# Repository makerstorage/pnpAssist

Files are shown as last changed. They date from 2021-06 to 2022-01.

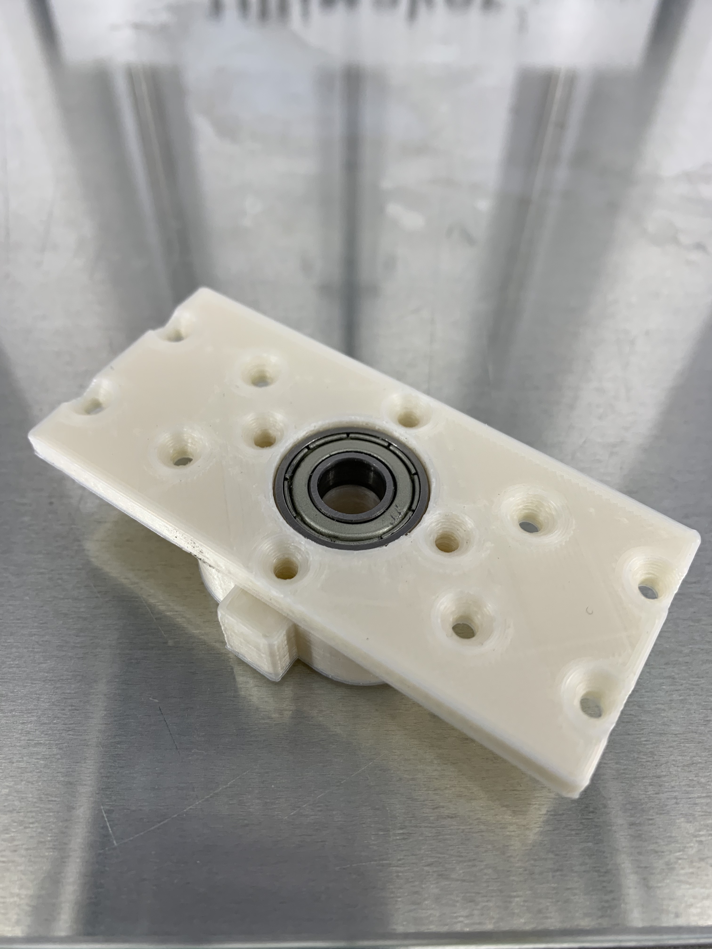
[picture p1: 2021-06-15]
images/IMG_0675.jpeg

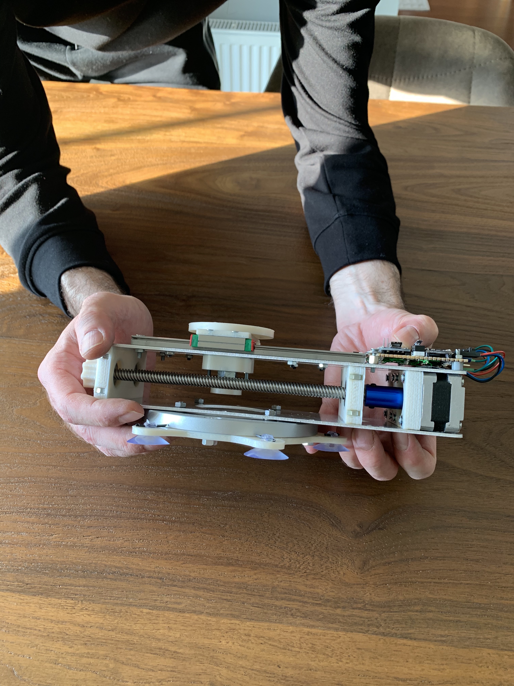
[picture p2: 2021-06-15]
images/IMG_0696.jpeg

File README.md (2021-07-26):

<!-- PROJECT LOGO 
<br />
<p align="center">
  <a href="https://github.com/github_username/repo_name">
    <img src="images/logo.png" alt="Logo" width="80" height="80">
  </a>
-->
  <h3 align="center">PnPAssist</h3>

<!-- ABOUT THE PROJECT -->
## Description
The PnPAssist is an open source innovative CNC table that position the next SMT component with a proper orientation for you to make hand assembly a lot more fun and way more efficient.

PnPAssist is a numerical, precise positioning device that makes tedious and repetitive manual PCB assembly easier for you and prevents you from making mistakes.

<!-- LICENSE -->
## License

GNU GENERAL PUBLIC LICENSE Version 3, 29 June 2007 See `LICENSE` for more information.

<!-- CONTRIBUTING -->
## Contributing

Contributions are what make the open source community such an amazing place to be learn, inspire, and create. Any contributions you make are **greatly appreciated**.

1. Fork the Project
2. Create your Feature Branch (`git checkout -b feature/AmazingFeature`)
3. Commit your Changes (`git commit -m 'Add some AmazingFeature'`)
4. Push to the Branch (`git push origin feature/AmazingFeature`)
5. Open a Pull Request

<!-- CONTACT -->
## Contact

Nuri Erginer - [@nerginer](https://twitter.com/nerginer) 
email - ne@makerstorage.com
Project Link: [Hackaday.io](https://hackaday.io/project/179878-pnpassist)

MakerStorage invests time and resources providing this open source design, please support MakerStorage and open-source hardware by purchasing products from MakerStorage!

Designed by MakerStorage LLC.

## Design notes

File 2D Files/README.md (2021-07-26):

Attention:
You may need to countersink some holes for proper assembly.

Material and production :

Laser cut from 2mm Aluminum

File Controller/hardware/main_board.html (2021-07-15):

Partlist exported from /Users/nerginer/electronics/pnpAssist/Controller/hardware/main_board.sch at 7/12/21 7:53 PM

Qty | Value | Device | Package | Parts | Description | POPULARITY
1 | | J2X5MM | 05C | J1 | Jumper switch 2 x 2.5 mm | 0
1 | | LED0805 | LED-0805 | 12V | LEDs
1 | | ML6 | ML6 | ICSP | HARTING
2 | | PINHD-1X3 | 1X03 | JP1, JP5 | PIN HEADER
6 | | SJ | SJ | SJ1, SJ2, SJ3, SJ4, SJ5, SJ6 | SMD solder JUMPER | 33
1 | 0.1uF | C-USC0805K | C0805K | C2 | CAPACITOR, American symbol
4 | 100nF | CAP0805 | 0805 | C3, C5, C8, C14 | Capacitor
5 | 100uF | CPOL-EUE3.5-8 | E3,5-8 | C4, C6, C7, C9, C10 | POLARIZED CAPACITOR, European symbol
2 | 10K | R-US_R0805 | R0805 | R2, R3 | RESISTOR, American symbol
1 | 10K | RESISTOR | 0805 | R7 | Resistor
1 | 10uF/10V | CPOL-USA/3216-18R | A/3216-18R | C1 | POLARIZED CAPACITOR, American symbol
1 | 16MHZ | CRYSTALHC49S | HC49/S | Q4 | CRYSTAL
2 | 16pf | CAP0805 | 0805 | C12, C13 | Capacitor
1 | 1K | R-US_R0805 | R0805 | R1 | RESISTOR, American symbol
1 | 2.2K | RESISTOR | 0805 | R9 | Resistor
2 | 2133-DRV8825 | 2133-DRV8825 | DRV8825 | IC_A_MOTOR, IC_B_MOTOR | DRV8825 Stepper Motor Driver Carrier, High Current
1 | 2PIN | 2PIN | B2B-PH-K-S | JP4
1 | 330r | R-US_R0805 | R0805 | R10 | RESISTOR, American symbol
1 | 4050D | 4050D | SO16 | IC2 | Hex non-inverting BUFFER
2 | 4PIN | 4PIN | B4B-PH-K-S | MOTOR-A, MOTOR-B
1 | 7805DT | 7805DT | TO252 | IC1 | Positive VOLTAGE REGULATOR
1 | ATMEGA328 | ATMEGA168 | TQFP32-08 | IC5
1 | DISPLAY-OLED-128X64-I2C | DISPLAY-OLED-128X64-I2C | DISPLAY-OLED-128X64-I2C | U$1 | 128x64 Dot Matrix OLED Module based on SSD1306 chip
1 | LP298XS | LP298XS | SOT23-5L | IC3
1 | MICROSD | MICROSD | MICROSD | X1 | Micro-SD / Transflash card holder with SPI pinout
1 | MST2V | MST2V | MSTBV2 | X4 | PHOENIX
1 | RED | LEDCHIP-LED0805 | CHIP-LED0805 | ACT | LED
1 | S_TACT | SPST_TACT-EVQQ2 | EVQ-Q2 | SW_NEXT | SMT 6mm switch, EVQQ2 series

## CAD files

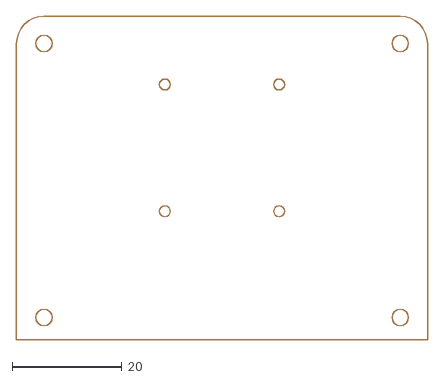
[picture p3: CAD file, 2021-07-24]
Controller/hardware/main_board.dxf
75.0 x 59.0

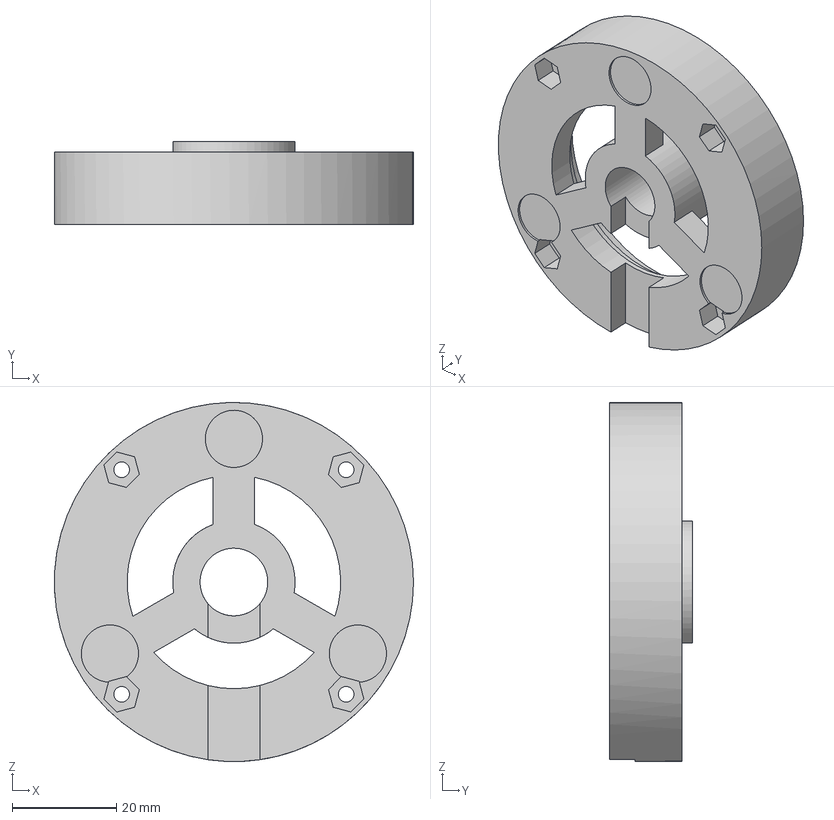
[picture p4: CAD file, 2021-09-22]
V2/3D Files/Step/main_base v29.step
69.0 x 16.0 x 69.0 mm

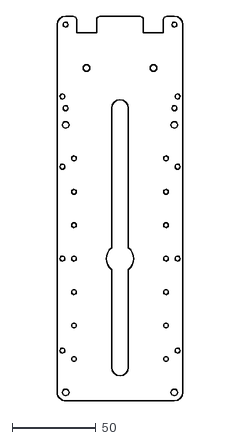
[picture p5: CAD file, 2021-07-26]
2D Files/top_sheet_metal.dxf
75.0 x 230.0

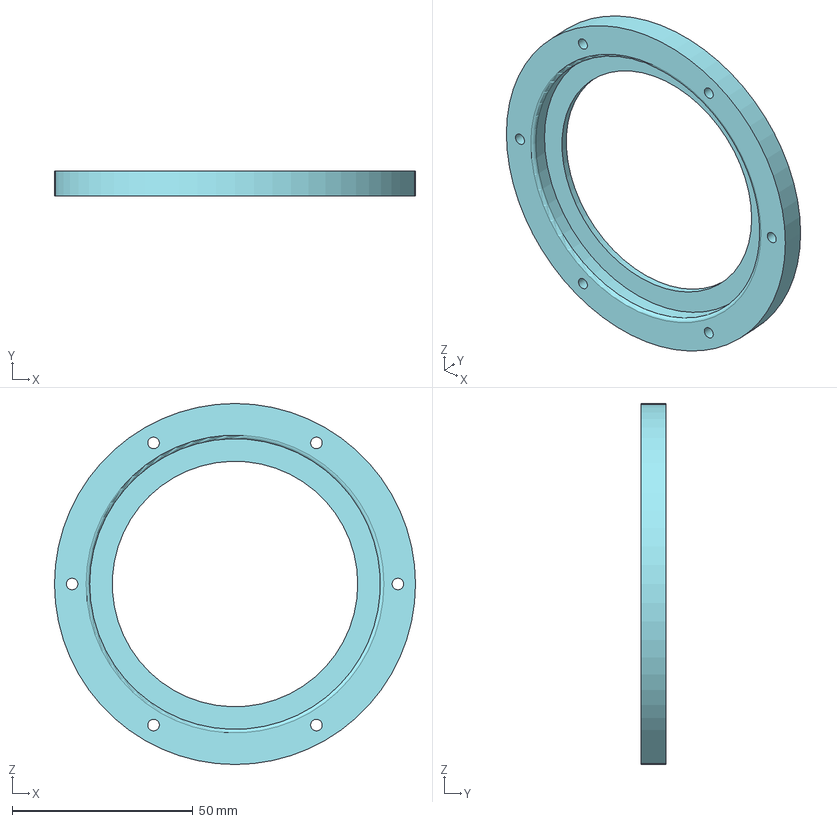
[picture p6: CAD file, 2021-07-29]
3d Files/step/buyuk_rulman_kapak.stp
100.0 x 7.00 x 100.0 mm

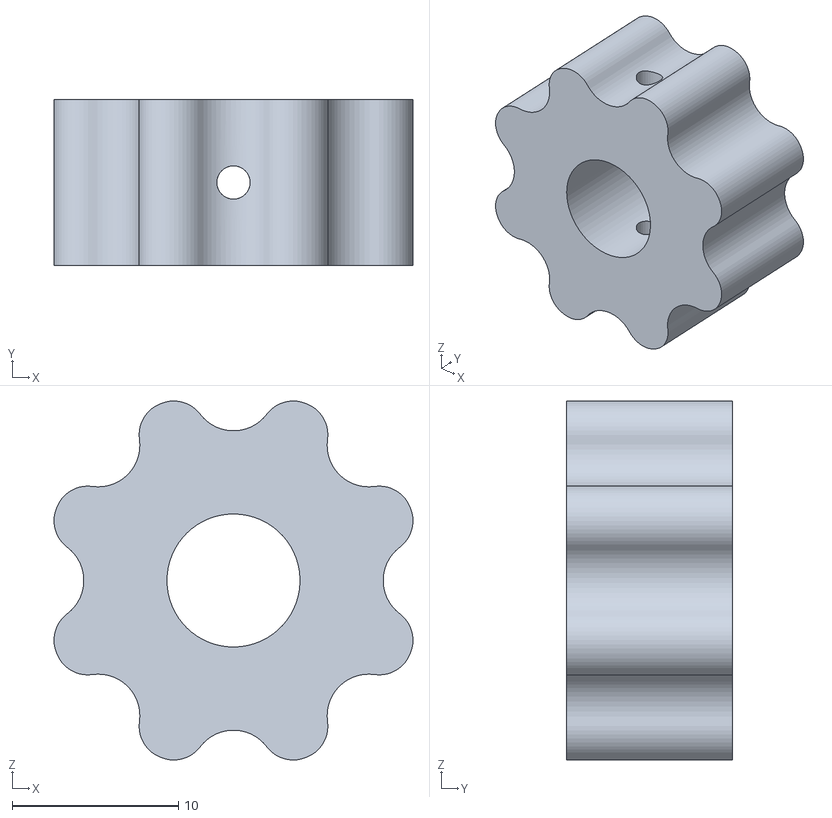
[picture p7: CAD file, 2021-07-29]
3d Files/stl/pnp_assist_tutac v1.stl
21.6 x 10.0 x 21.6

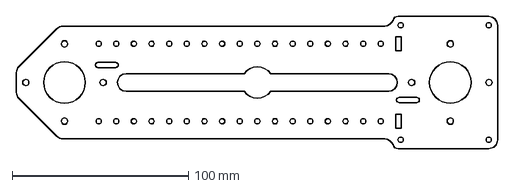
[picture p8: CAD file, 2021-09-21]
V2/2D Files/sac.dxf
272.8 x 75.0 mm

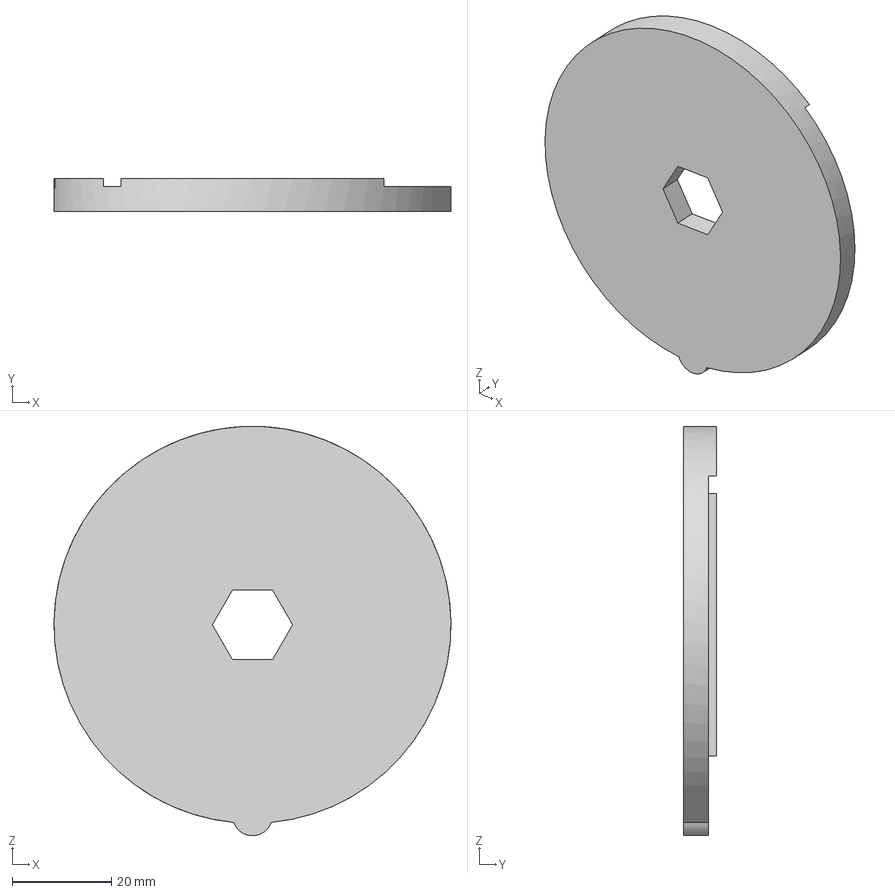
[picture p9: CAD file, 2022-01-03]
V2/3D Files/Step/rotator5.step
80.0 x 6.60 x 82.5 mm

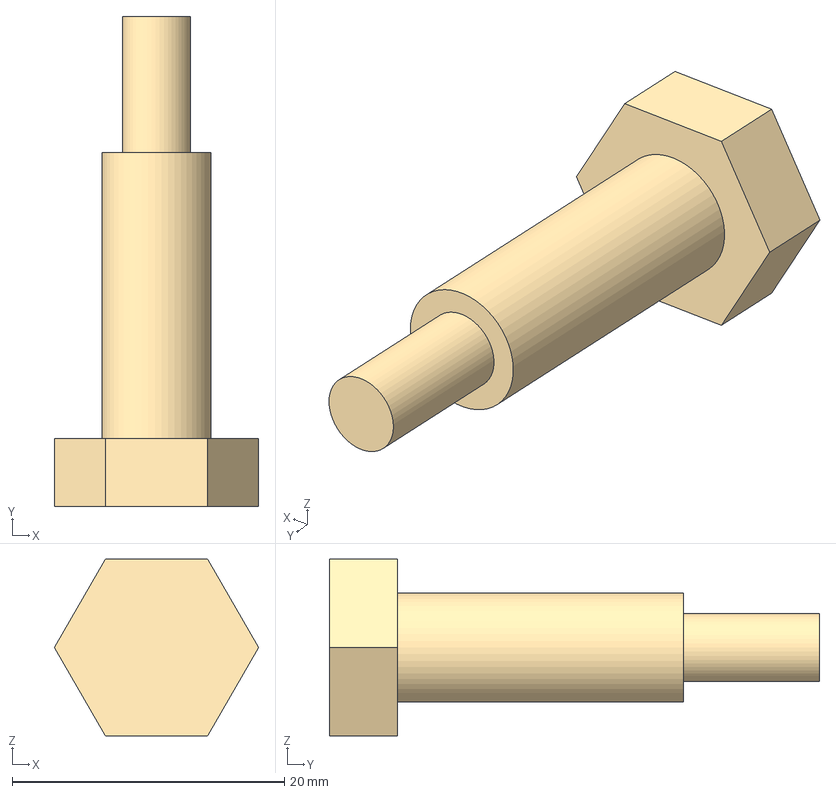
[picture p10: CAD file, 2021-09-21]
V2/CNC/custom_shaft.step
15.0 x 36.0 x 13.0 mm

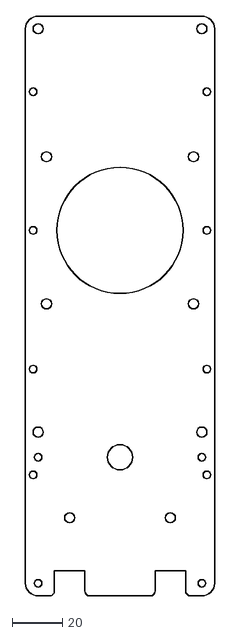
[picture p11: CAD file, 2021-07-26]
2D Files/bottom_sheet_metal.dxf
75.0 x 230.0

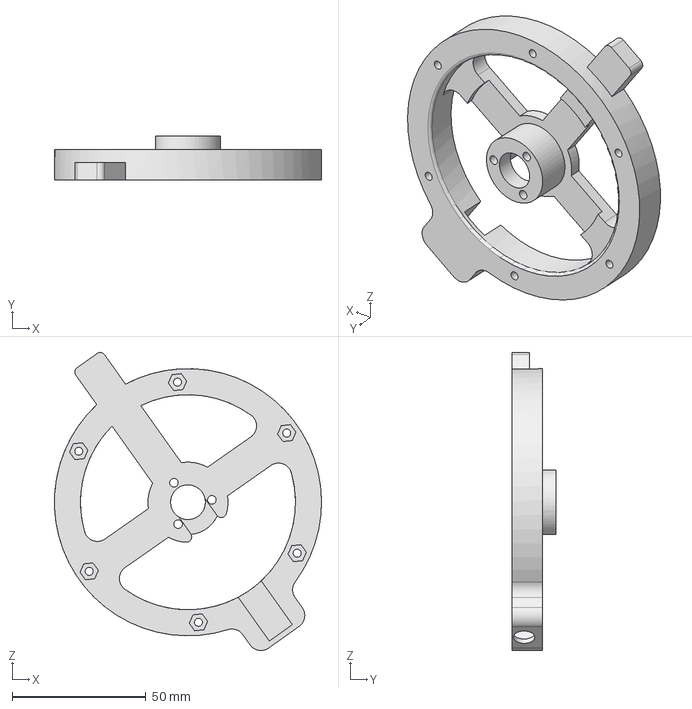
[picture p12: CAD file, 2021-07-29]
3d Files/step/buyuk_rulman_tut.stp
100.0 x 16.5 x 111.6 mm

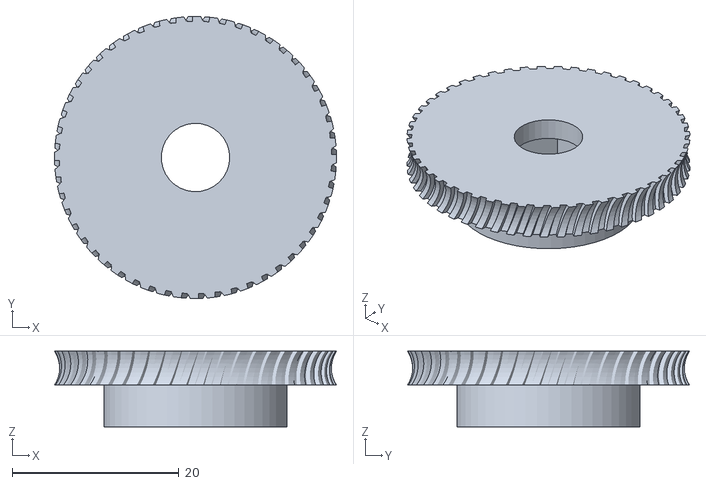
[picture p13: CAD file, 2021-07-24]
3d Files/stl/son_disli_kavisli v2.stl
33.8 x 33.8 x 9.06

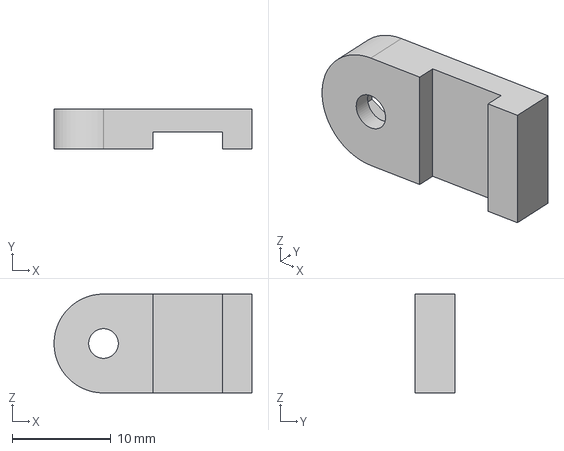
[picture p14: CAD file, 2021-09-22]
V2/3D Files/Step/kablo_bastir v2.step
20.0 x 4.00 x 10.0 mm

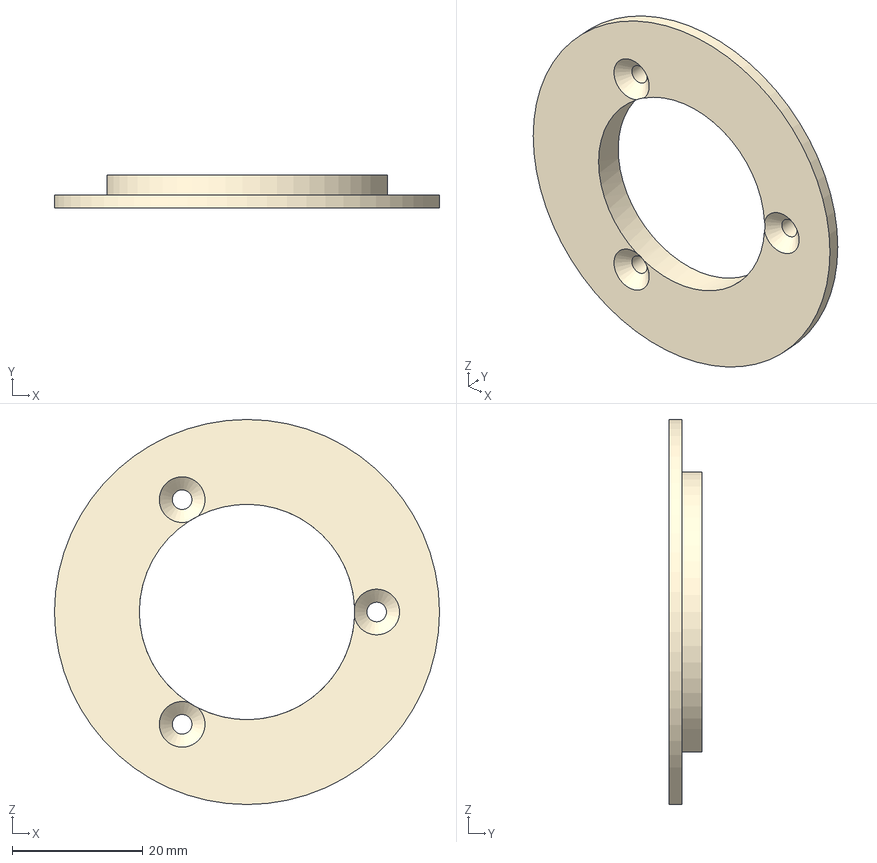
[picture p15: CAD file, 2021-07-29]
3d Files/step/ayak_ust_base.stp
59.0 x 5.00 x 59.0 mm

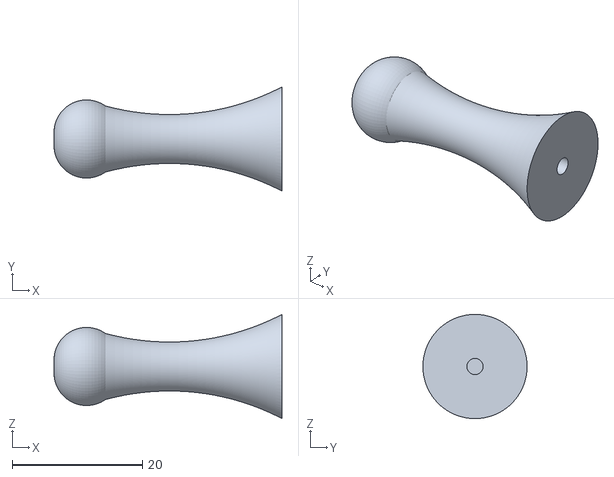
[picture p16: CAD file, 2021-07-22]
3d Files/stl/tutcak.stl
35.0 x 16.0 x 16.0

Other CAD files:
V2/3D Files/Step/yukselti v7.step
3d Files/step/rulmanlik.stp
3d Files/stl/bilezik.stl
V2/3D Files/Step/bearing_cap v2.step
3d Files/step/ayak_ust_base_B.stp
3d Files/step/motor_tut.stp
3d Files/step/rotator3.stp
3d Files/step/rulman_tut_orta.stp
3d Files/step/ust_arabalik.stp
3d Files/step/ust_rulmanlik3.stp
3d Files/stl/ayak_ust_base.stl
3d Files/stl/ayak_ust_base_B.stl
3d Files/stl/buyuk_rulman_kapak.stl
3d Files/stl/buyuk_rulman_tut.stl
3d Files/stl/lead t8 2mm pitch-duz_hex v1.stl
3d Files/stl/motor_tut.stl
3d Files/stl/rotator3.stl
3d Files/stl/rulman_tut.stl
3d Files/stl/rulman_tut_orta.stl
3d Files/stl/rulmanlik.stl
3d Files/stl/ust_arabalik.stl
3d Files/stl/ust_rulmanlik3.stl
V2/3D Files/Step/alt_rulmanlik v13.step
V2/3D Files/Step/arabalik v16.step
V2/3D Files/Step/bearing_inner v14.step
V2/3D Files/Step/carousel2 v7.step
V2/3D Files/Step/clips v2.step
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

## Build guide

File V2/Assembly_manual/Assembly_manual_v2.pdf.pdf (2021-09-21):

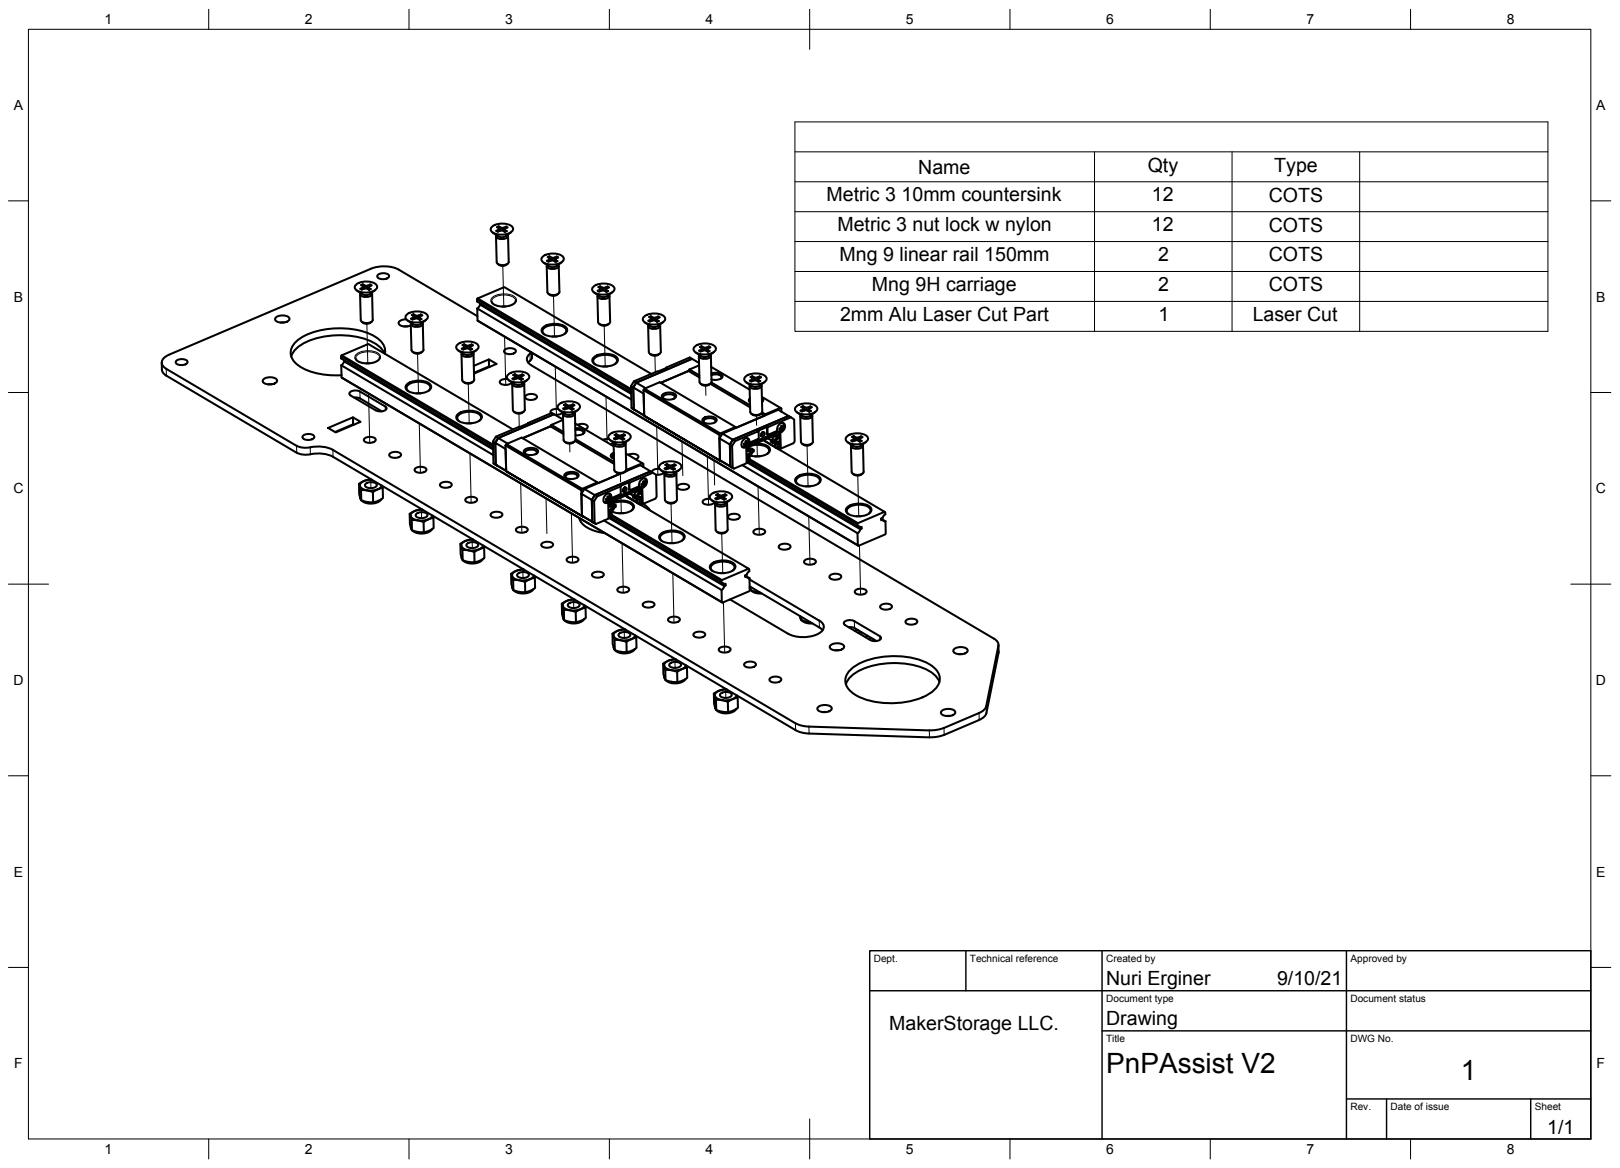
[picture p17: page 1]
Name; Qty; Type; Metric 3 10mm countersink; COTS; Metric 3 nut lock w nylon; Mng 9 linear rail 150mm; Mng 9H carriage; 2mm Alu Laser Cut Part; Laser Cut; Dept.; Technical reference; Created by; Approved by; Document type; Document status; Title; DWG No.; Rev.; Date of issue; Sheet; Drawing; PnPAssist V2; Nuri Erginer; MakerStorage LLC.

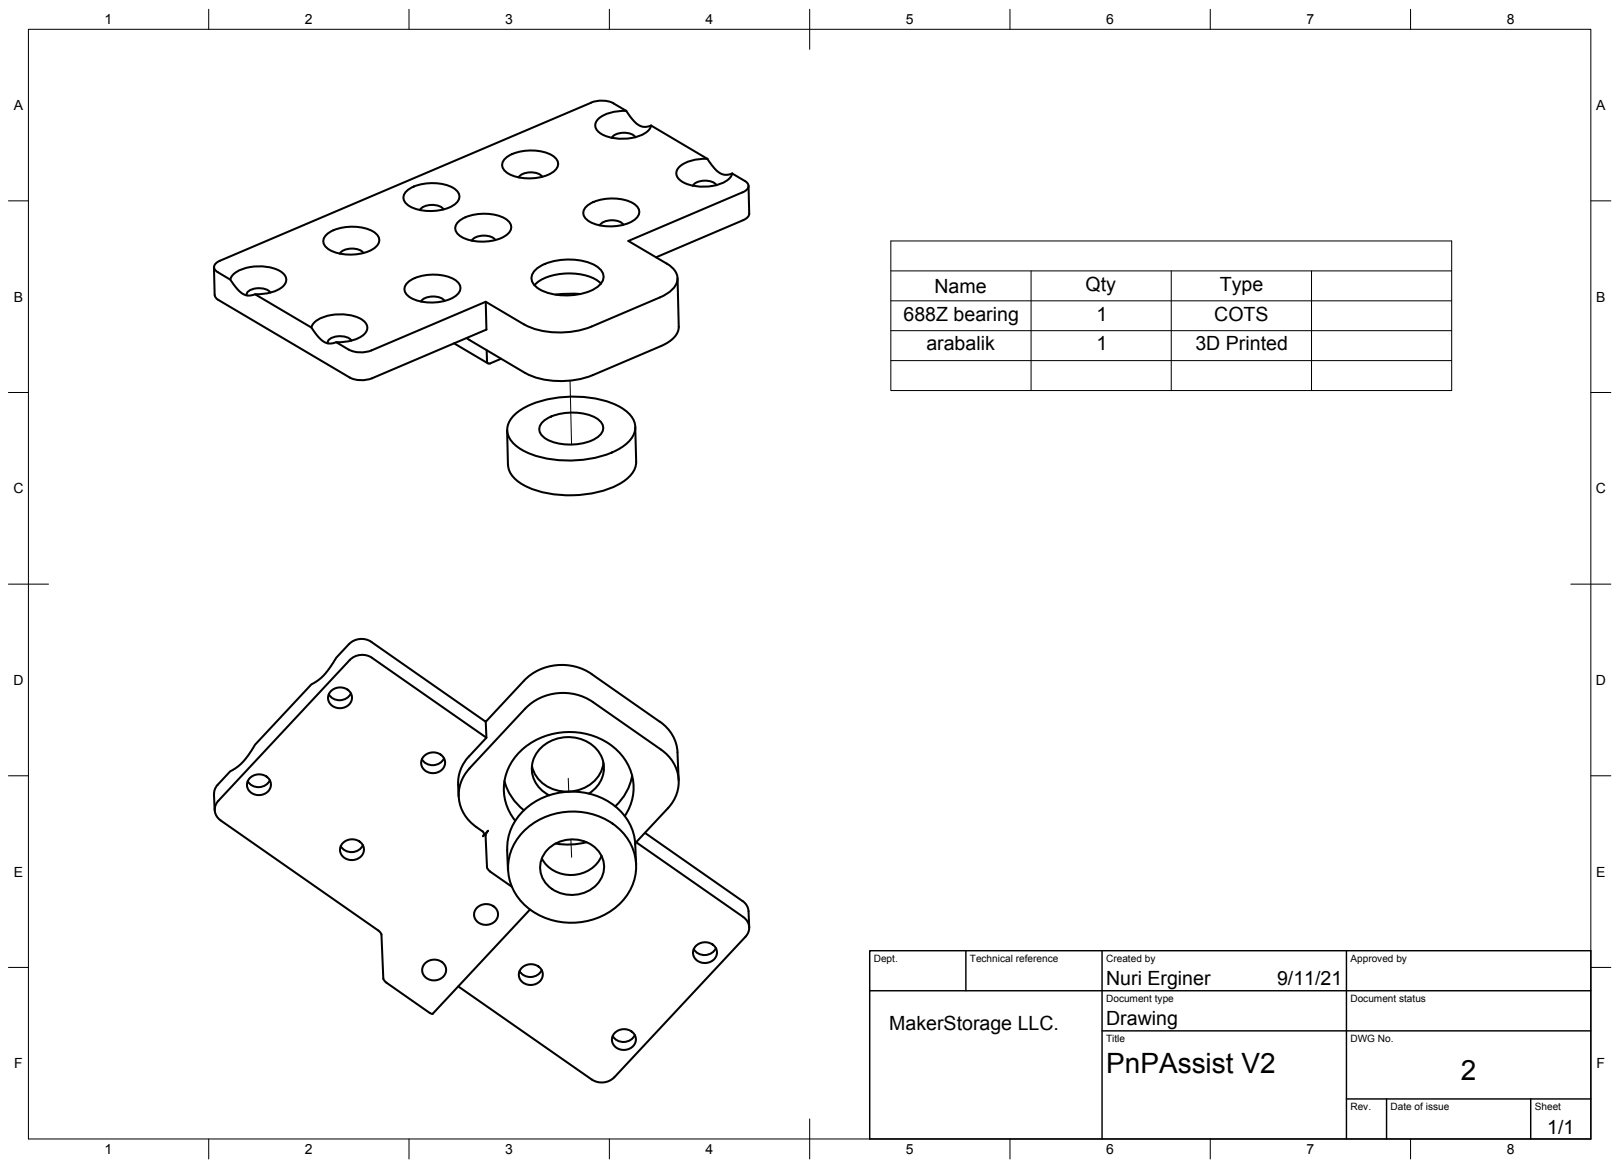
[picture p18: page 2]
Name; Qty; Type; 688Z bearing; COTS; arabalik; 3D Printed; Dept.; Technical reference; Created by; Approved by; Document type; Document status; Title; DWG No.; Drawing; PnPAssist V2; Nuri Erginer; MakerStorage LLC.

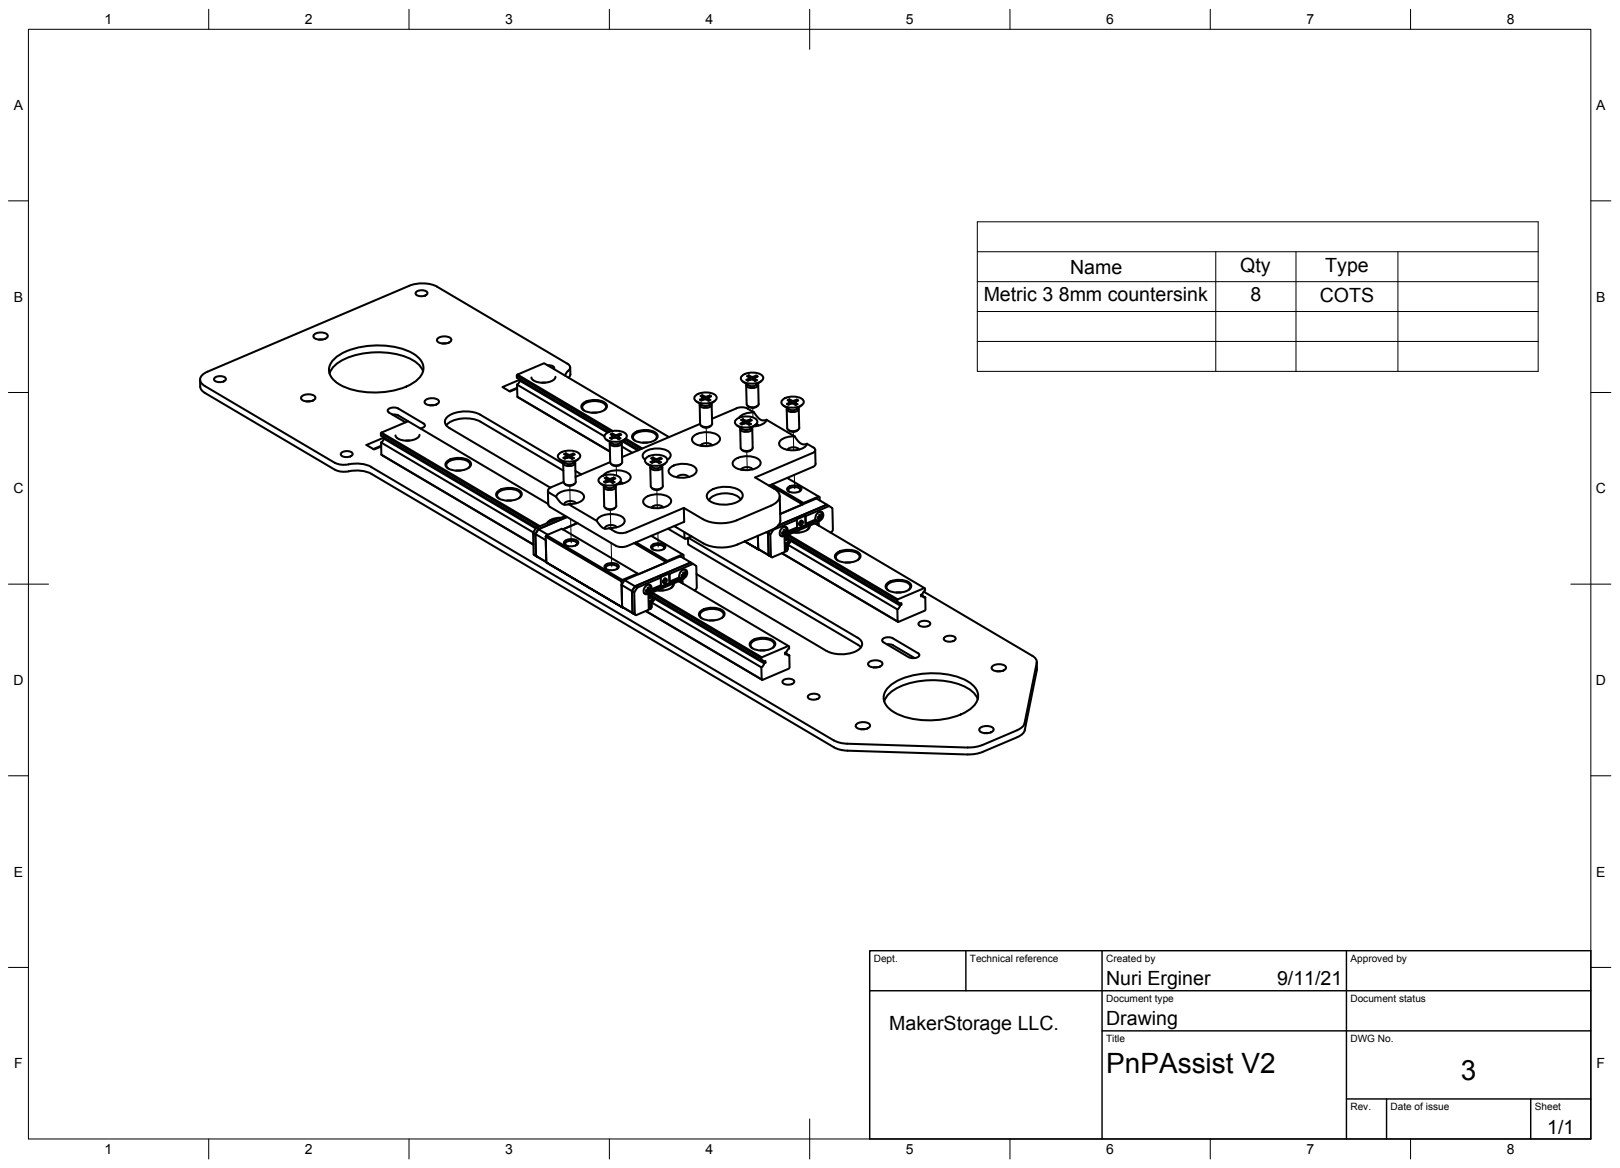
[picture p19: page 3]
Dept.; Technical reference; Created by; Approved by; Document type; Document status; Title; DWG No.; Drawing; PnPAssist V2; Nuri Erginer; Name; Qty; Type; Metric 3 8mm countersink; COTS; MakerStorage LLC.

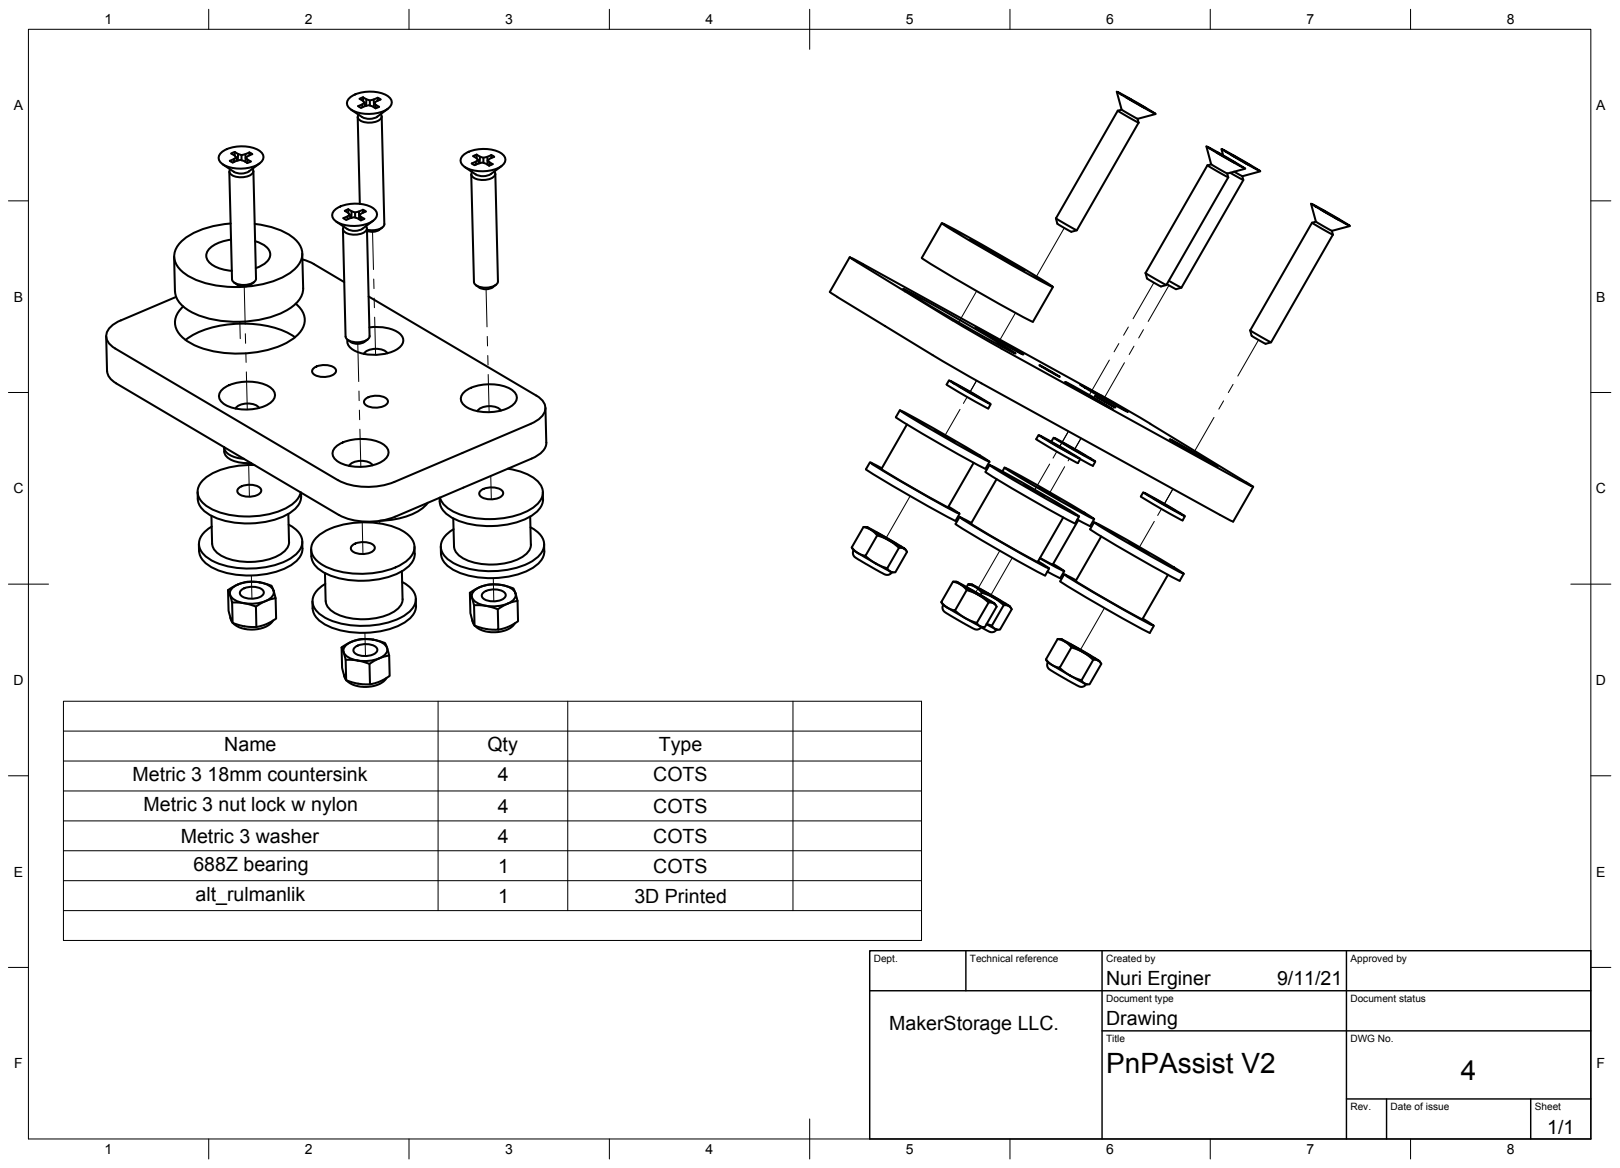
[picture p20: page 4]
Dept.; Technical reference; Created by; Approved by; Document type; Document status; Title; DWG No.; Drawing; PnPAssist V2; Nuri Erginer; alt_rulmanlik; 3D Printed; 688Z bearing; COTS; Metric 3 washer; Metric 3 nut lock w nylon; Metric 3 18mm countersink; Name; Qty; Type; MakerStorage LLC.

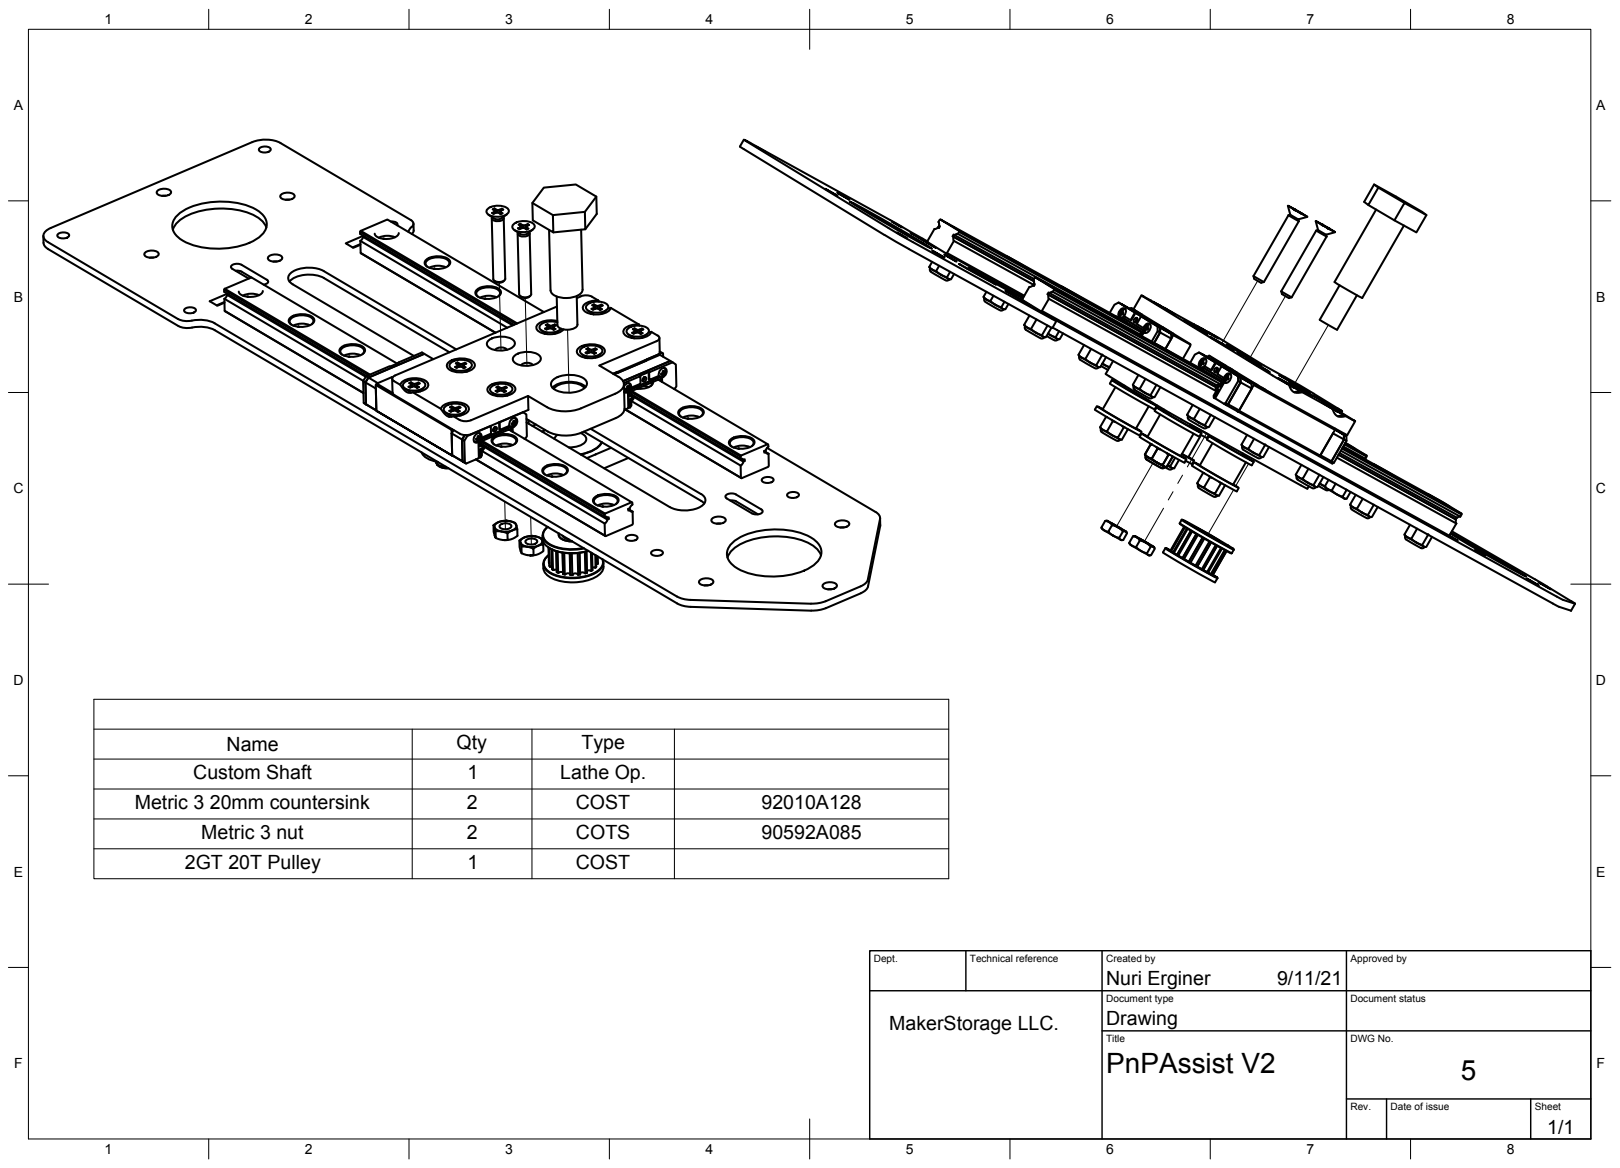
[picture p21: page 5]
Dept.; Technical reference; Created by; Approved by; Document type; Document status; Title; DWG No.; Drawing; PnPAssist V2; Nuri Erginer; Name; Qty; Type; Custom Shaft; Lathe Op.; Metric 3 20mm countersink; COST; Metric 3 nut; COTS; 2GT 20T Pulley; MakerStorage LLC.

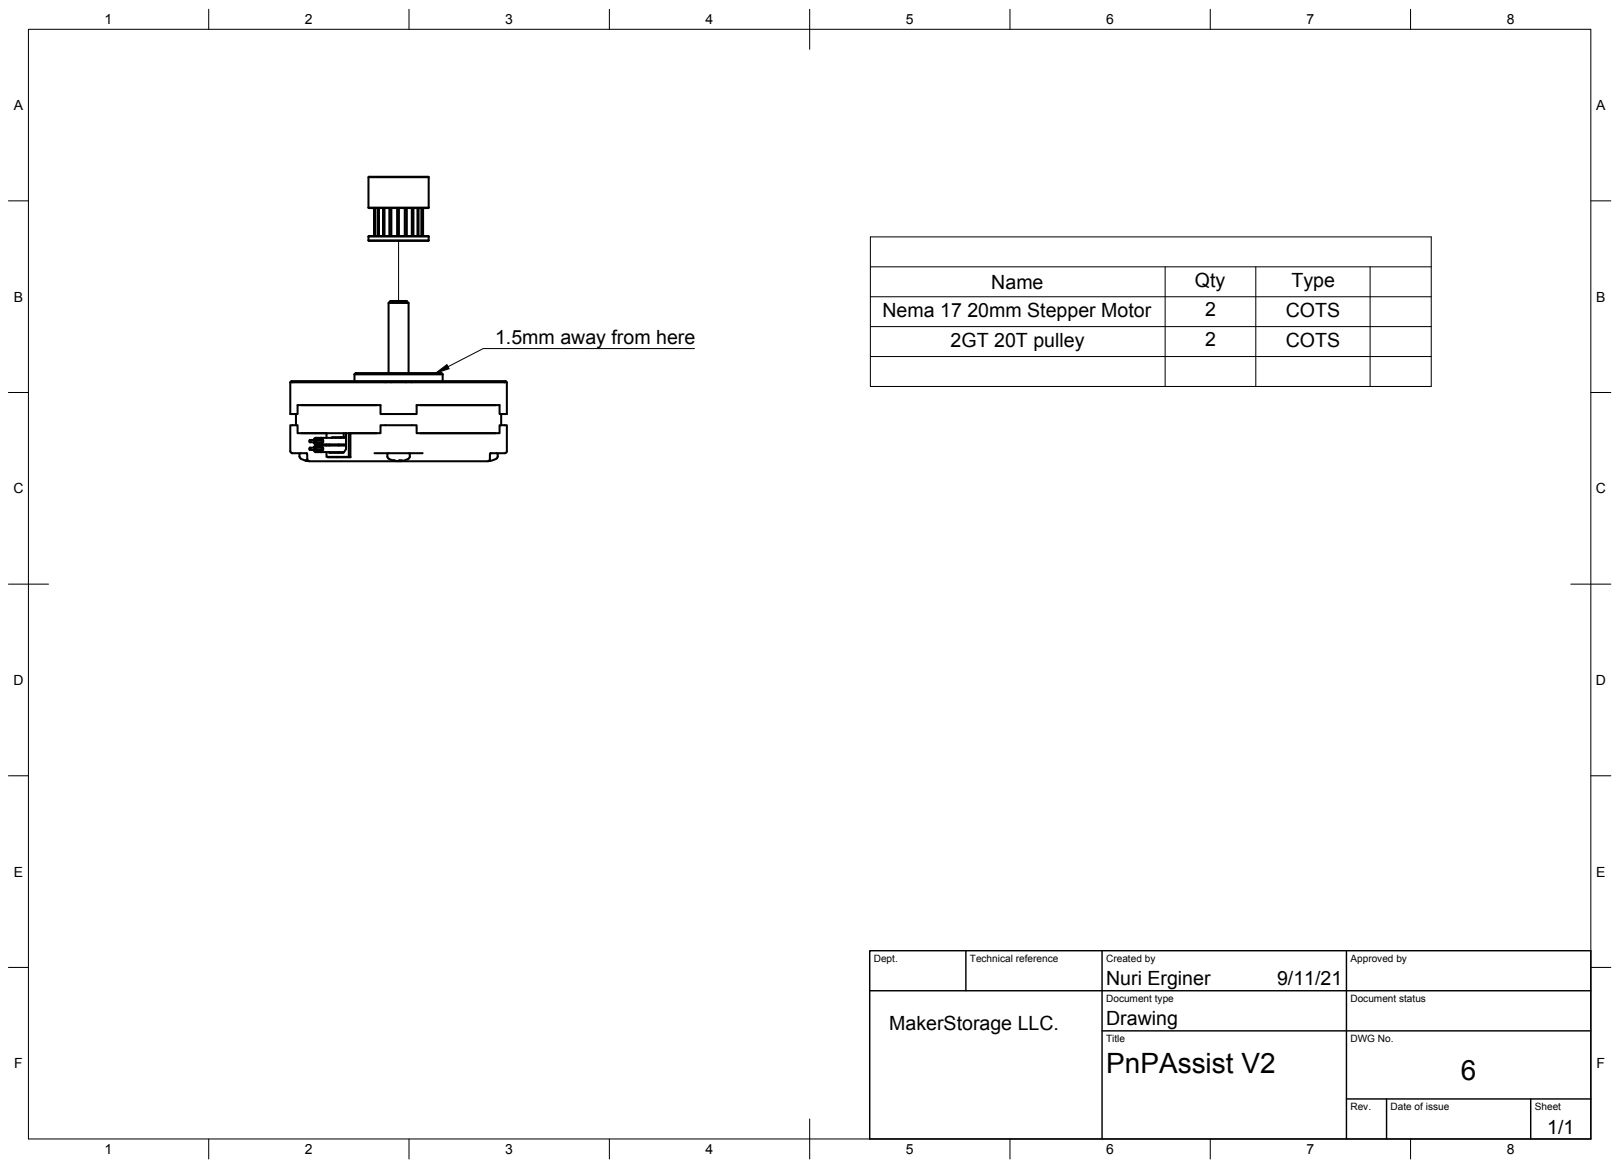
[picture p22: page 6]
Dept.; Technical reference; Created by; Approved by; Document type; Document status; Title; DWG No.; Drawing; PnPAssist V2; Nuri Erginer; Name; Qty; Type; Nema 17 20mm Stepper Motor; COTS; 2GT 20T pulley; MakerStorage LLC.

1.5mm away from here

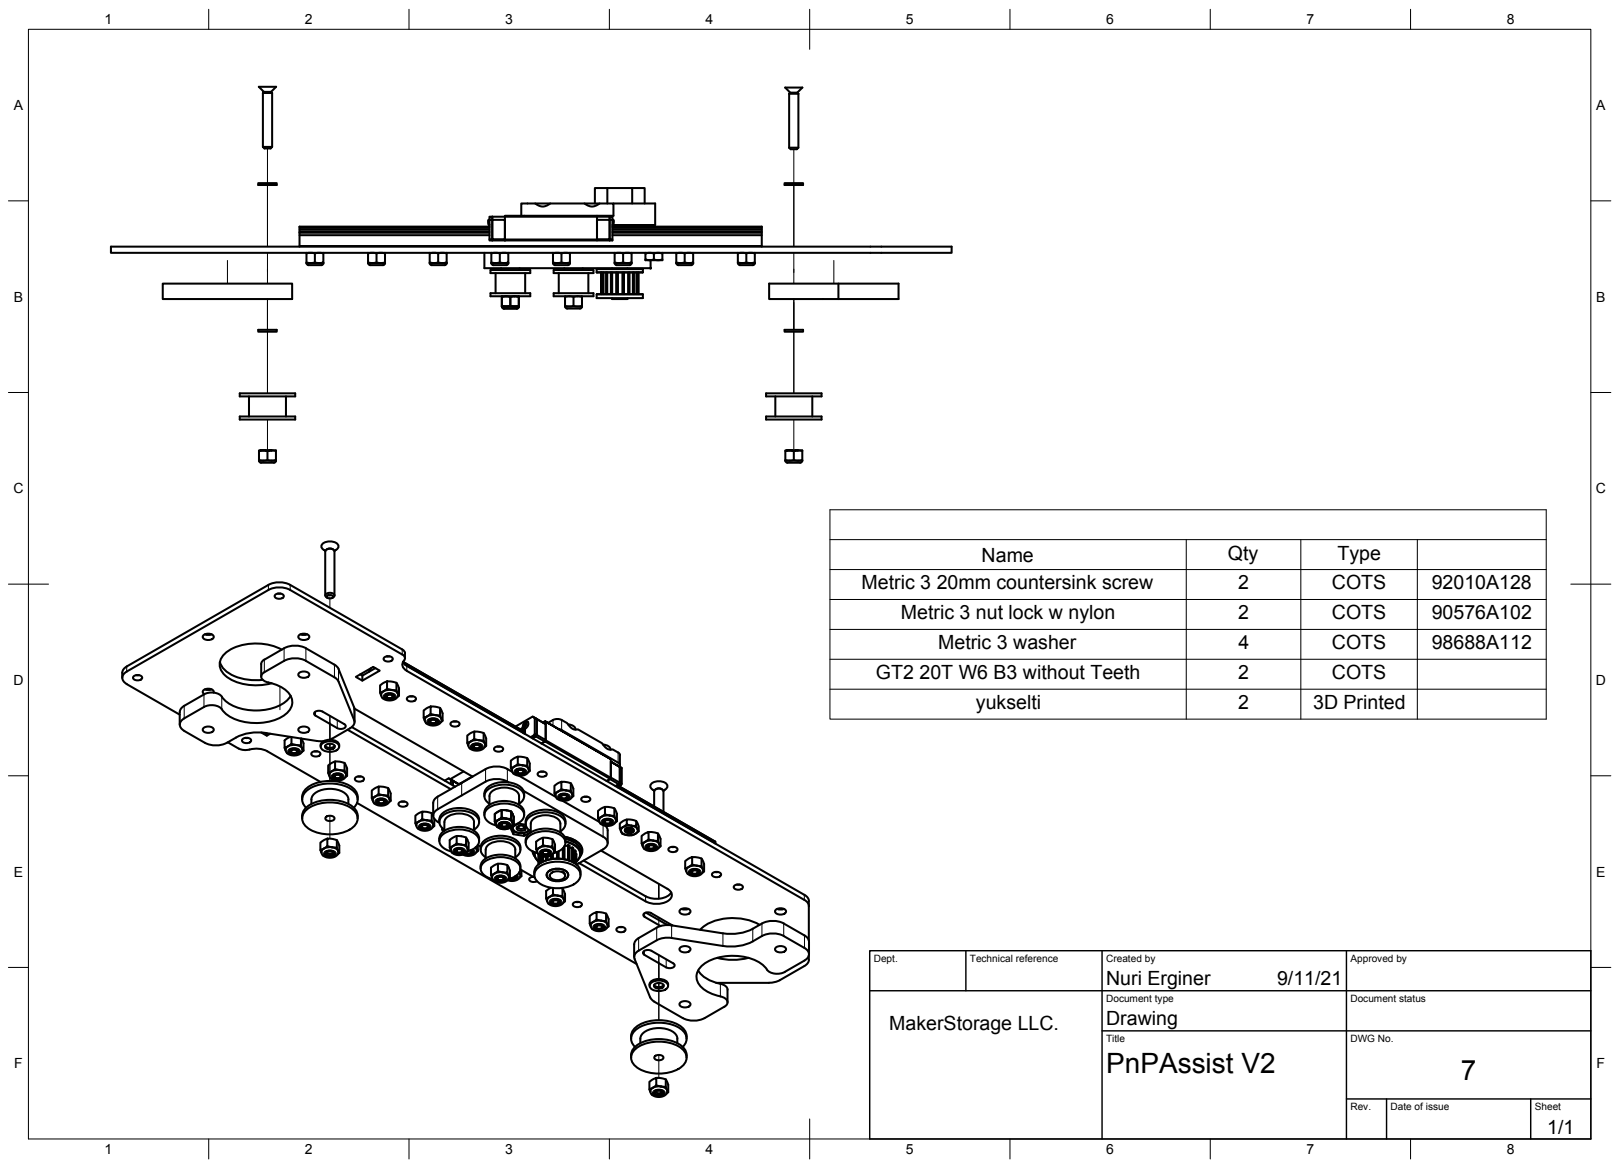
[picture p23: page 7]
Dept.; Technical reference; Created by; Approved by; Document type; Document status; Title; DWG No.; Drawing; PnPAssist V2; Nuri Erginer; Name; Qty; Type; Metric 3 20mm countersink screw; COTS; Metric 3 nut lock w nylon; Metric 3 washer; GT2 20T W6 B3 without Teeth; yukselti; 3D Printed; MakerStorage LLC.

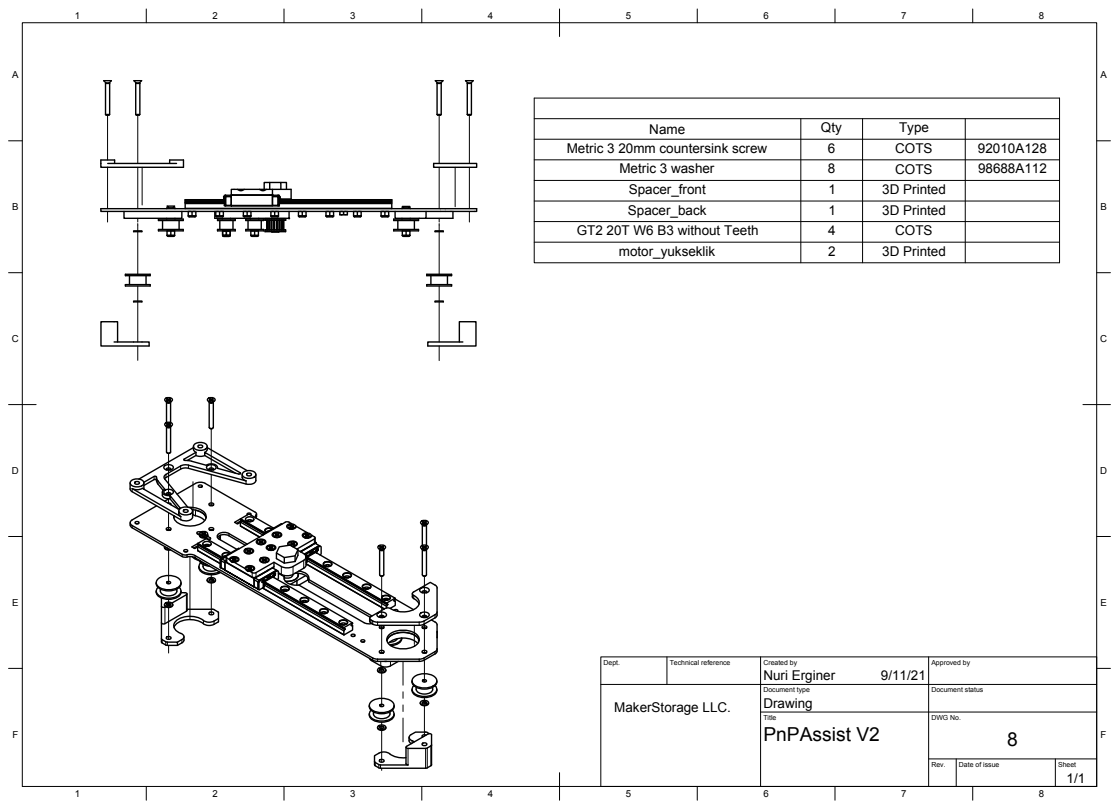
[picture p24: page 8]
Dept.; Technical reference; Created by; Approved by; Document type; Document status; Title; DWG No.; Drawing; PnPAssist V2; Nuri Erginer; Name; Qty; Type; Metric 3 20mm countersink screw; COTS; Metric 3 washer; Spacer_front; 3D Printed; Spacer_back; GT2 20T W6 B3 without Teeth; motor_yukseklik; MakerStorage LLC.

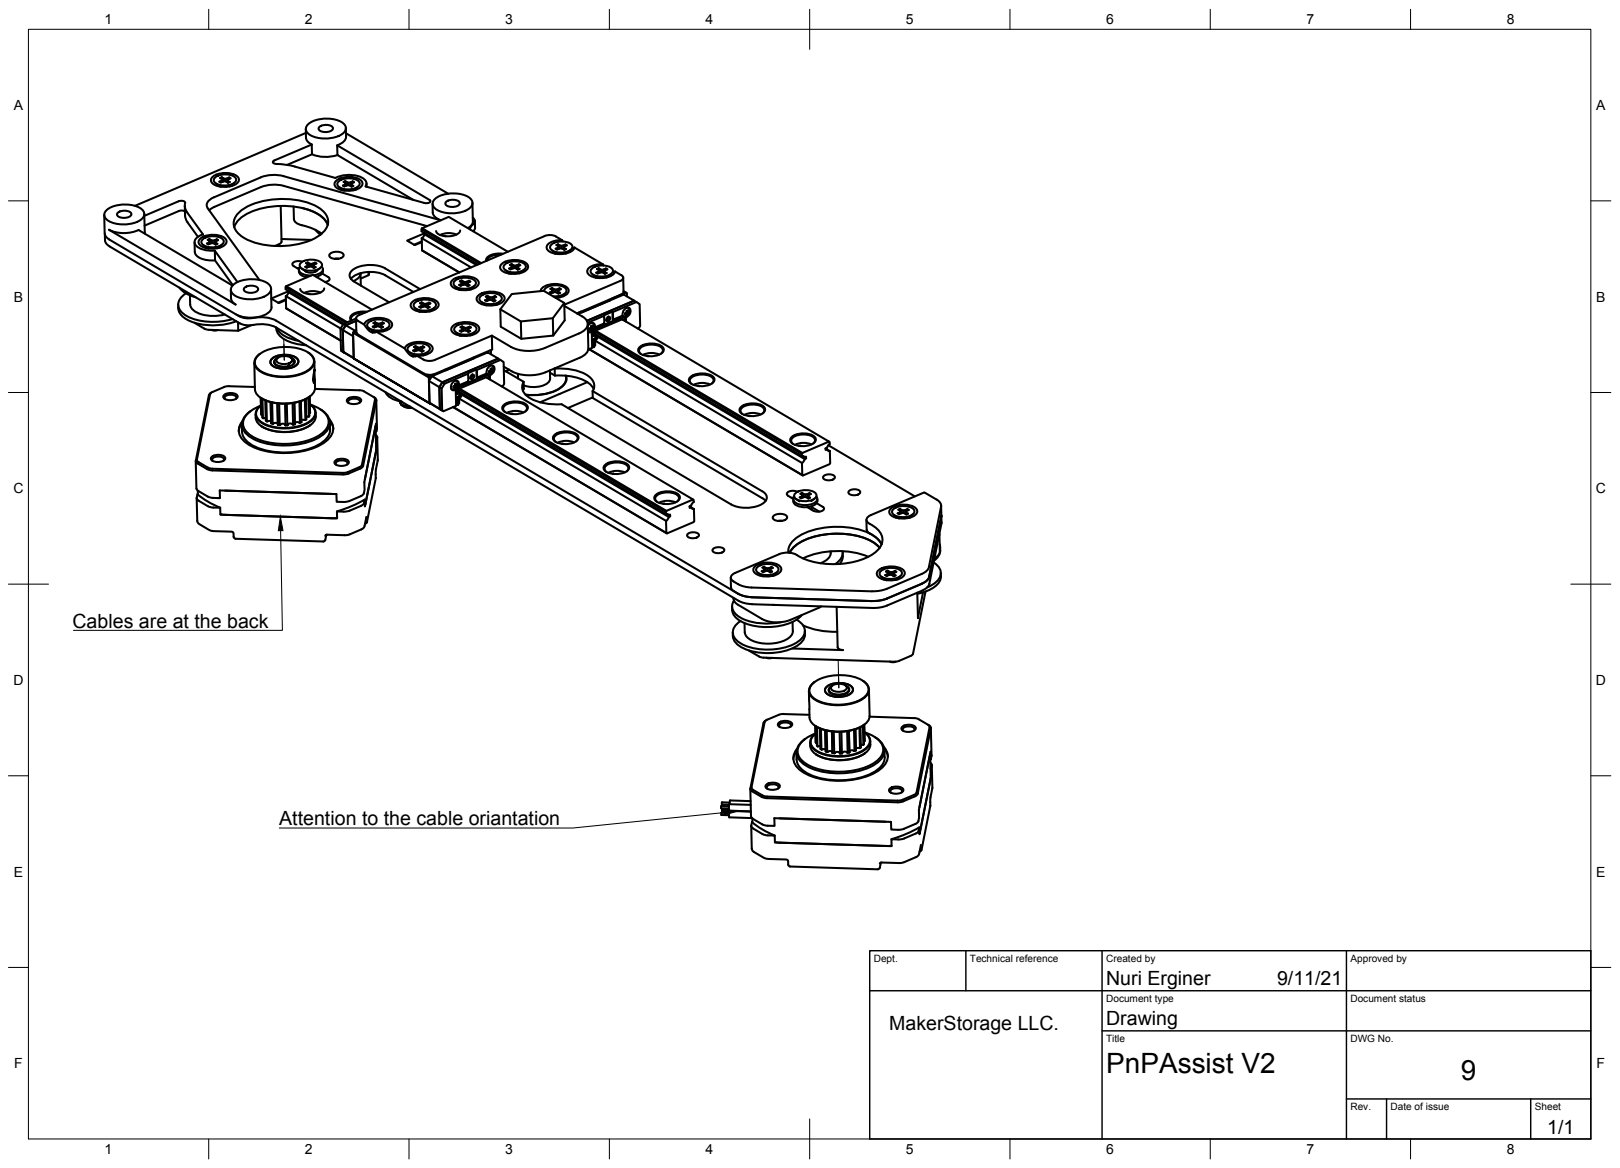
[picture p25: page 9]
Dept.; Technical reference; Created by; Approved by; Document type; Document status; Title; DWG No.; Drawing; PnPAssist V2; Nuri Erginer; MakerStorage LLC.

Cables are at the back

Attention to the cable oriantation

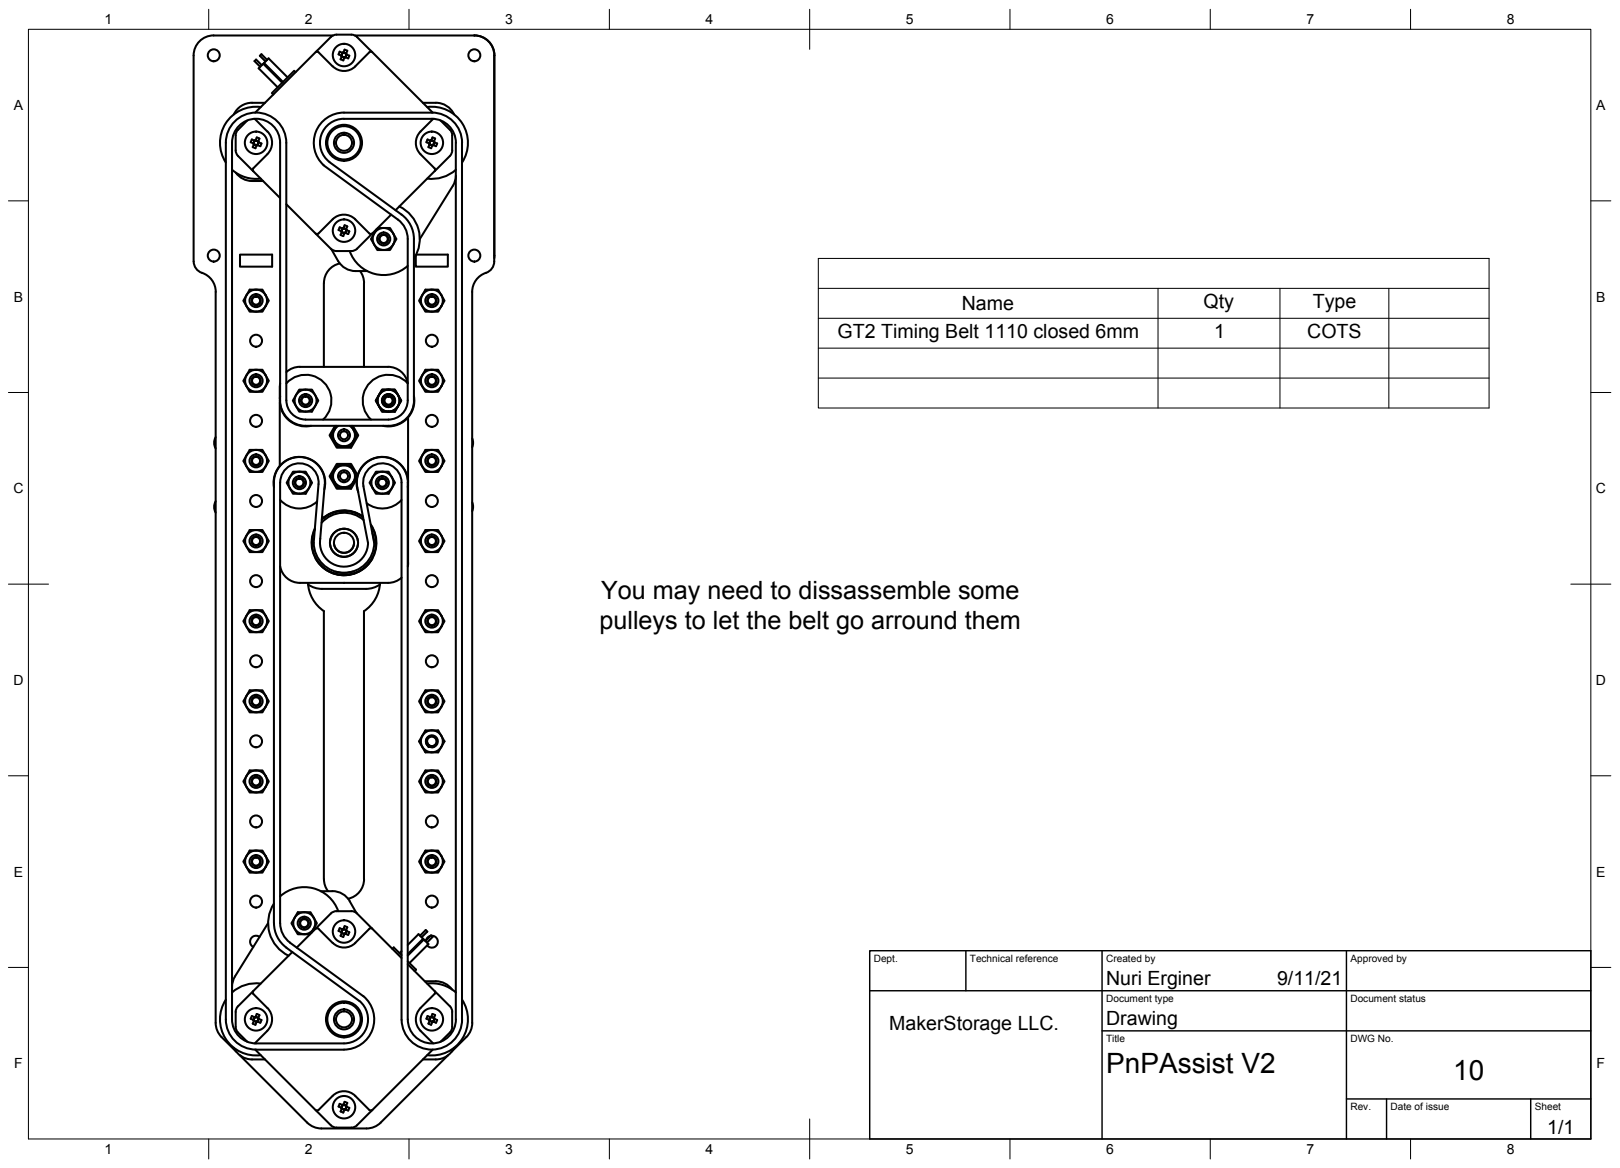
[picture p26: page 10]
Dept.; Technical reference; Created by; Approved by; Document type; Document status; Title; DWG No.; Drawing; PnPAssist V2; Nuri Erginer; Name; Qty; Type; GT2 Timing Belt 1110 closed 6mm; COTS; MakerStorage LLC.

You may need to dissassemble some
pulleys to let the belt go arround them

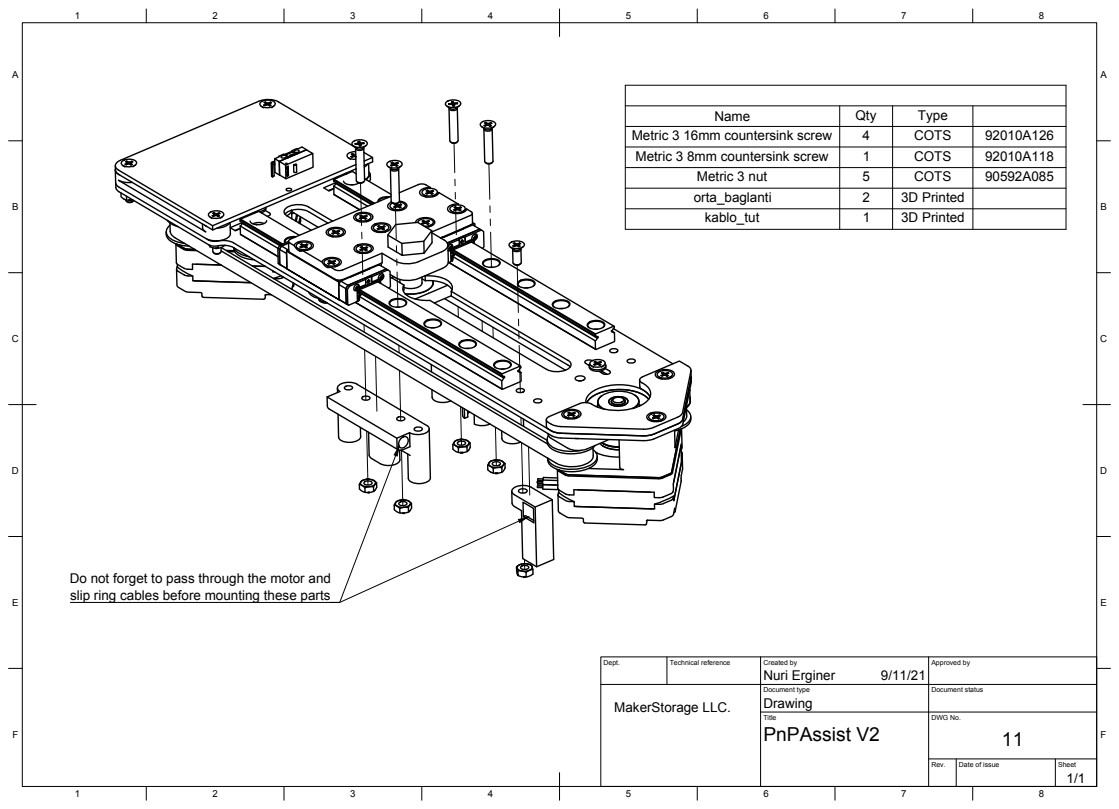
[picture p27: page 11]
Dept.; Technical reference; Created by; Approved by; Document type; Document status; Title; DWG No.; Drawing; PnPAssist V2; Nuri Erginer; Name; Qty; Type; Metric 3 16mm countersink screw; COTS; Metric 3 8mm countersink screw; Metric 3 nut; orta_baglanti; 3D Printed; kablo_tut; MakerStorage LLC.

Do not forget to pass through the motor and
slip ring cables before mounting these parts

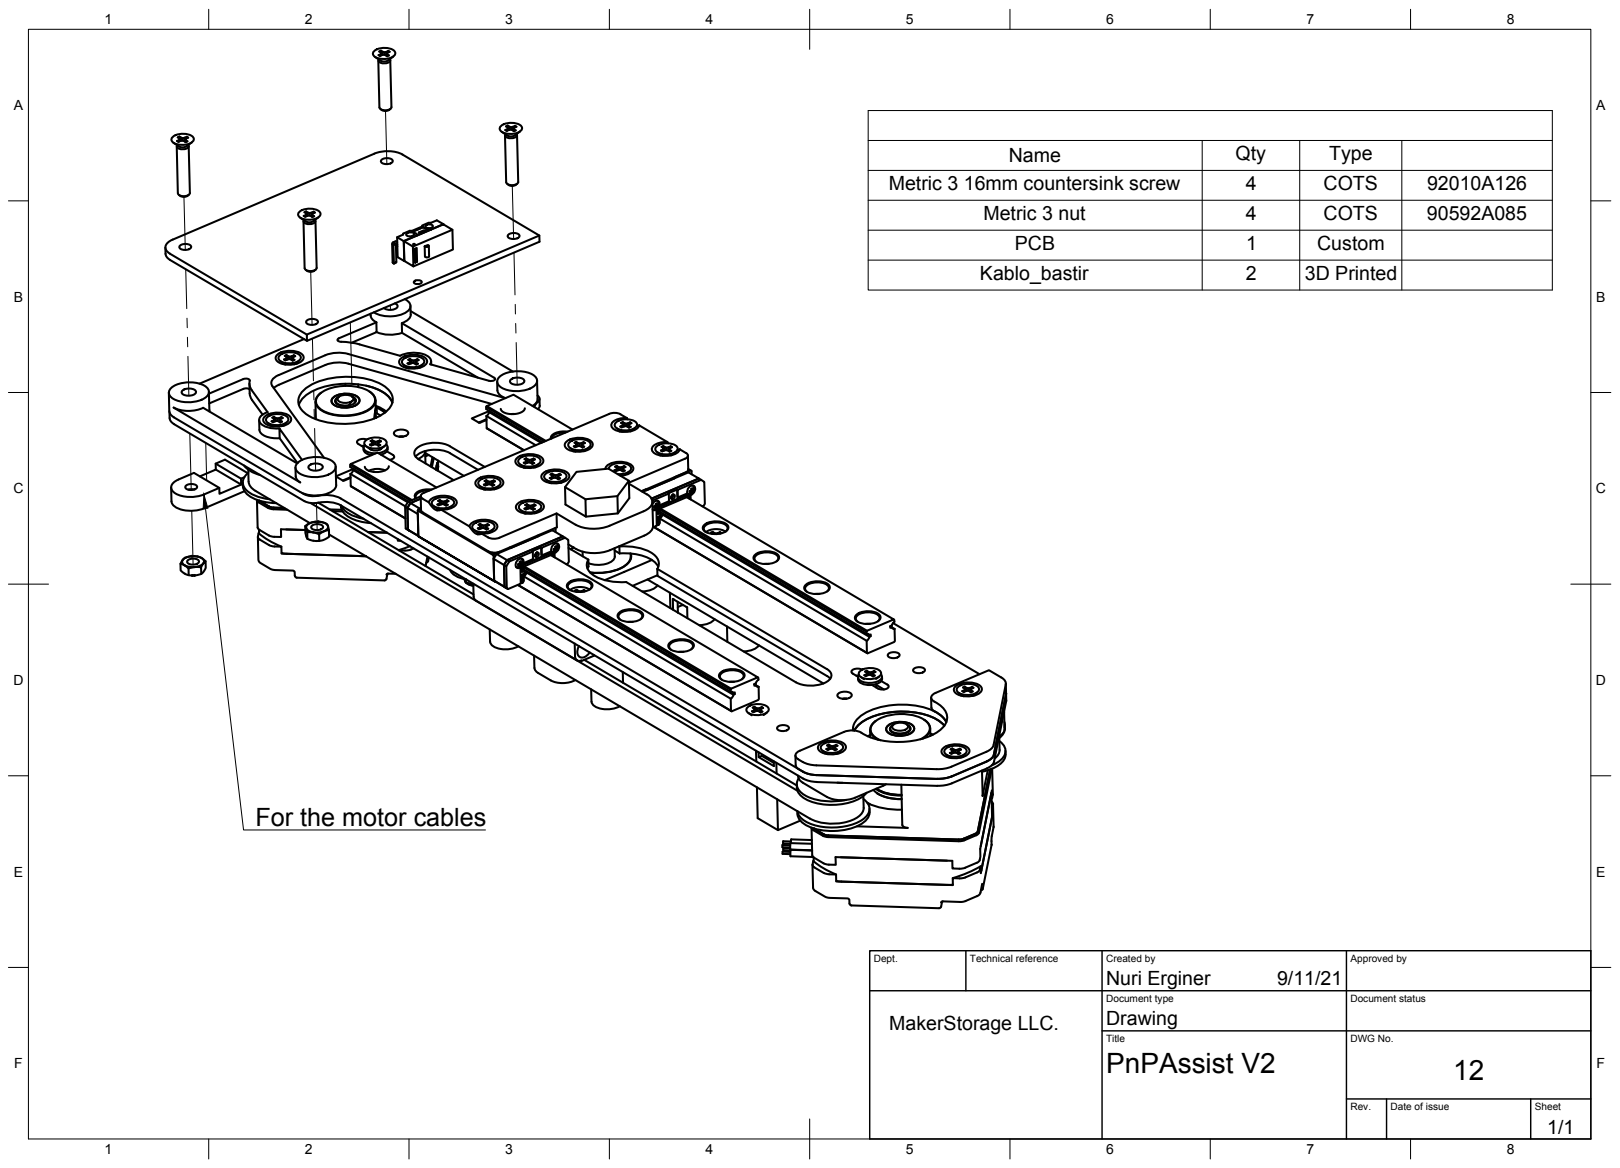
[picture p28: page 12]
Dept.; Technical reference; Created by; Approved by; Document type; Document status; Title; DWG No.; Drawing; PnPAssist V2; Nuri Erginer; Name; Qty; Type; Metric 3 16mm countersink screw; COTS; Metric 3 nut; PCB; Custom; Kablo_bastir; 3D Printed; MakerStorage LLC.

For the motor cables

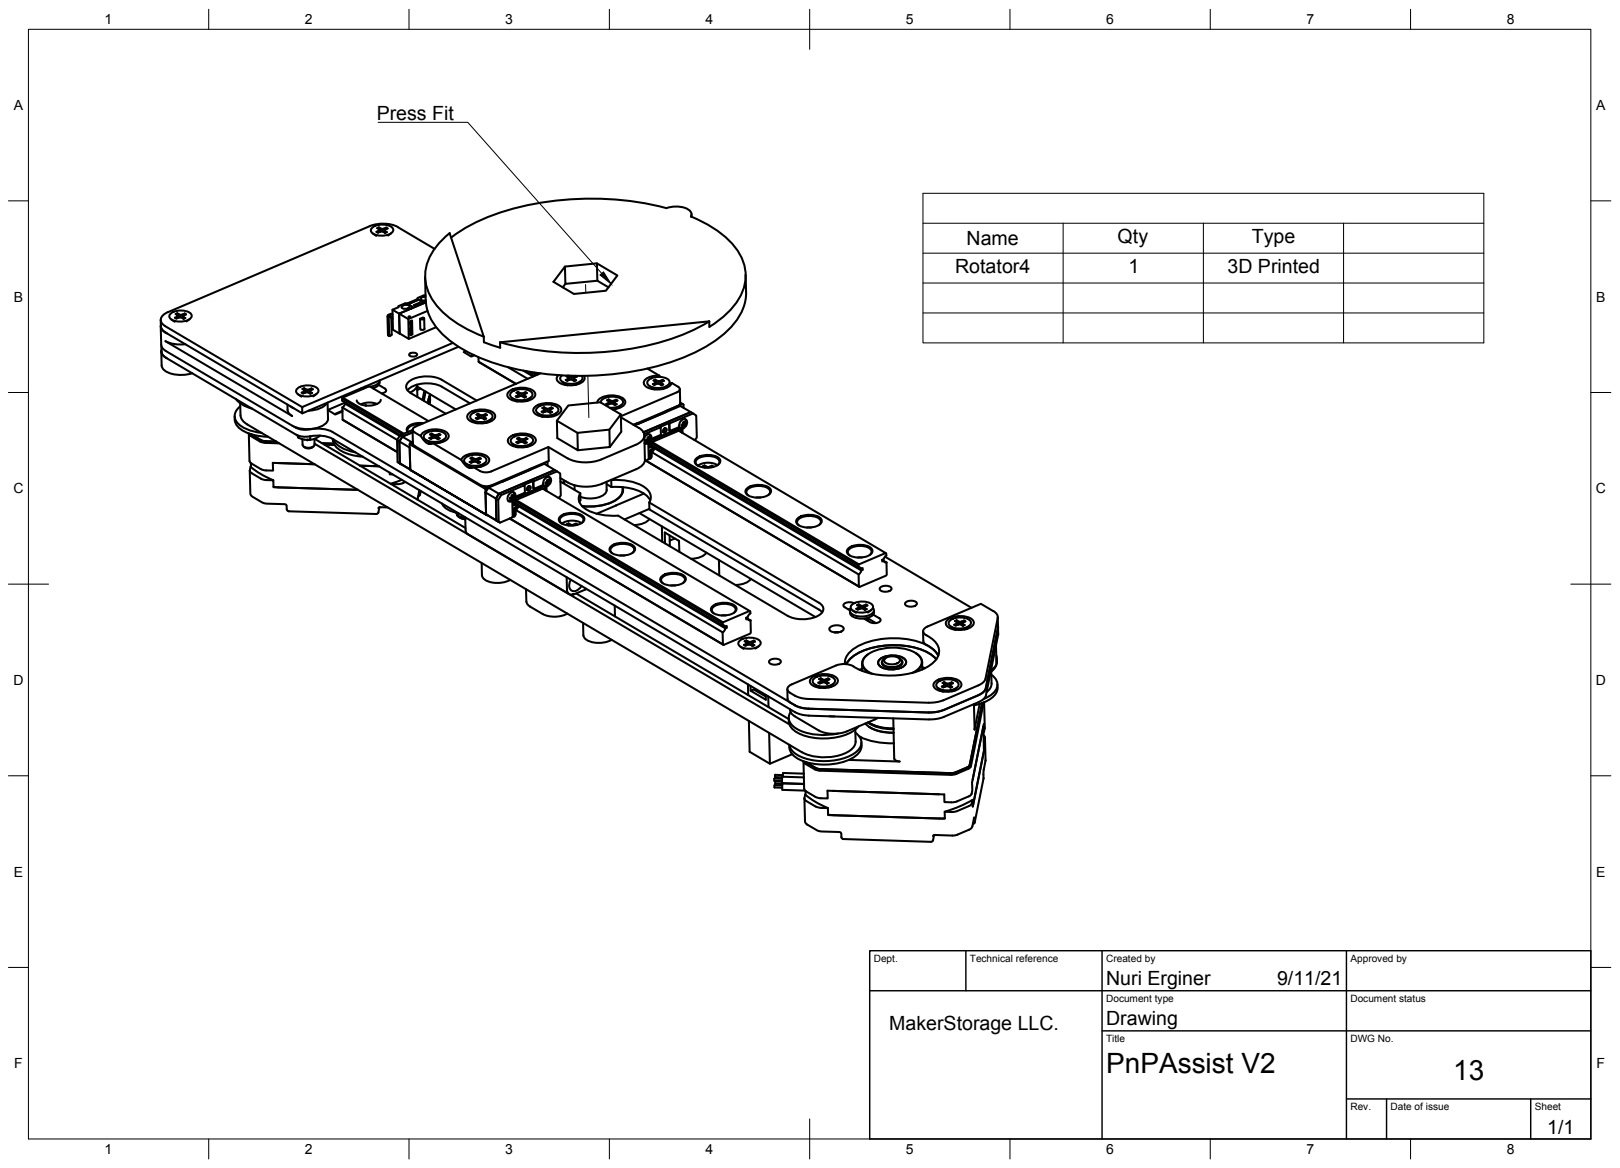
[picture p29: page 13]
Dept.; Technical reference; Created by; Approved by; Document type; Document status; Title; DWG No.; Drawing; PnPAssist V2; Nuri Erginer; Name; Qty; Type; Rotator4; 3D Printed; Press Fit; MakerStorage LLC.

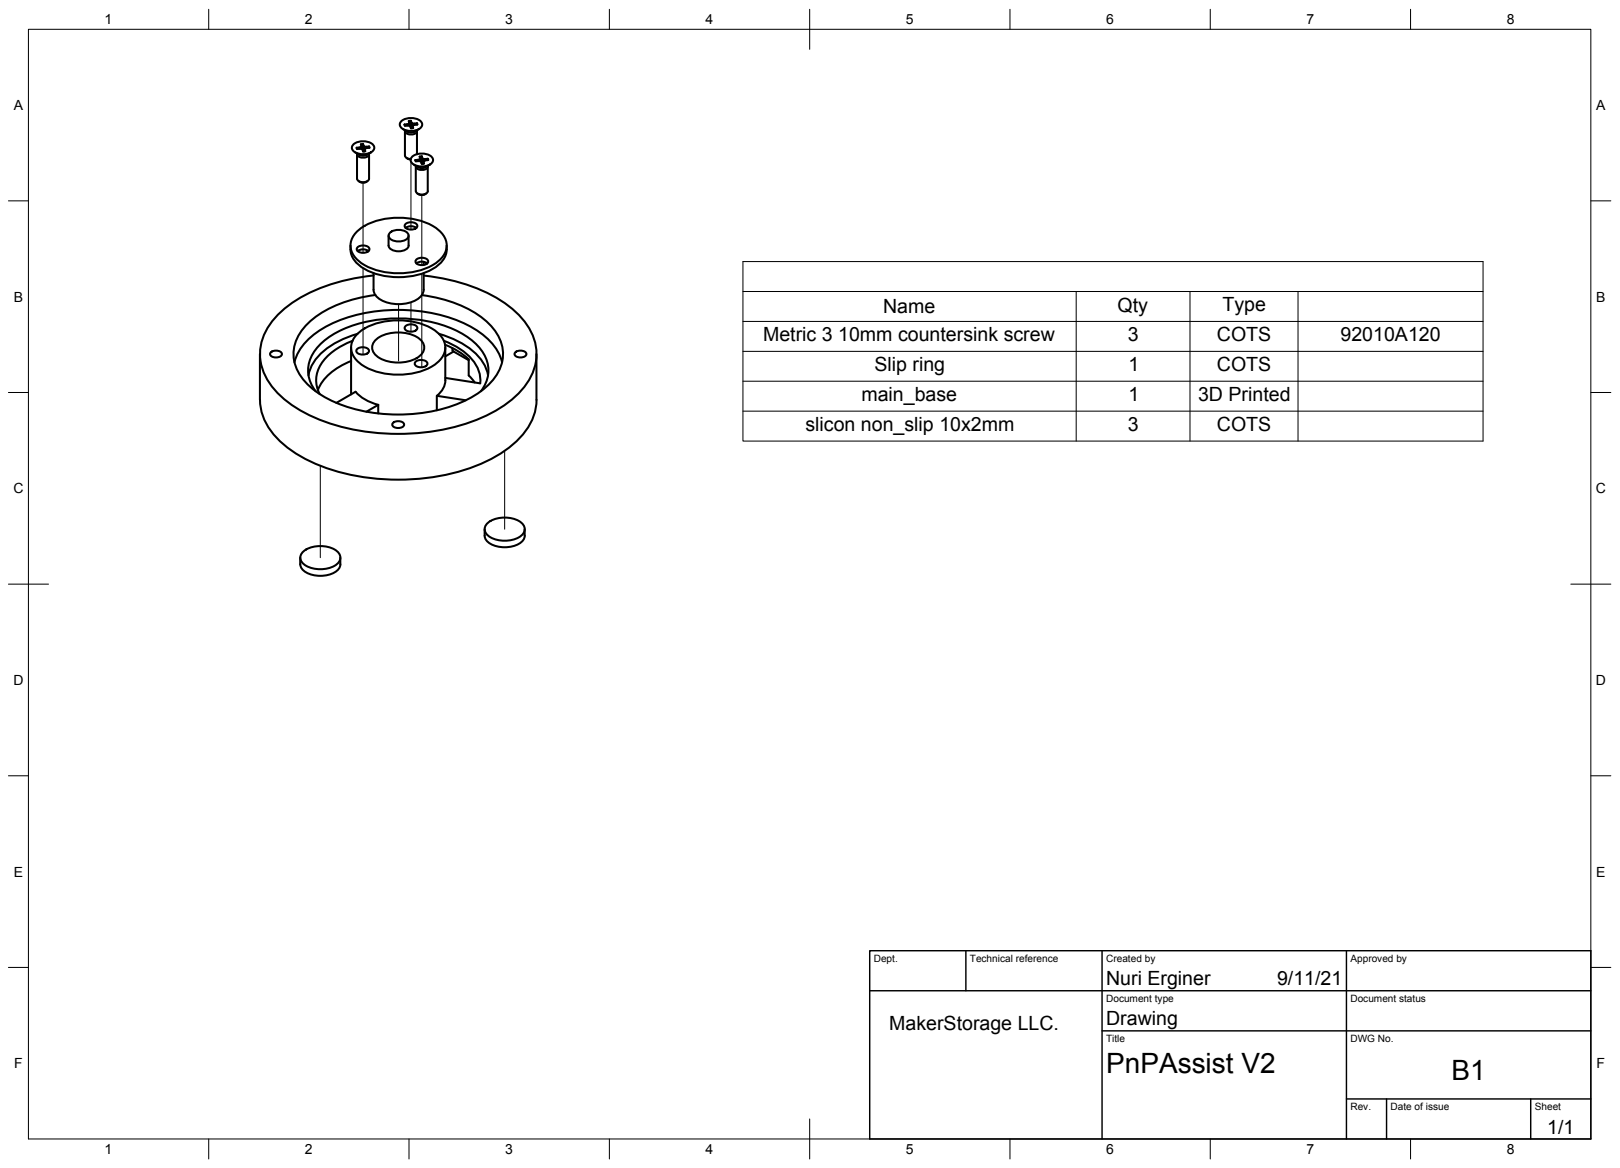
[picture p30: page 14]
Dept.; Technical reference; Created by; Approved by; Document type; Document status; Title; DWG No.; Drawing; PnPAssist V2; Nuri Erginer; Name; Qty; Type; Metric 3 10mm countersink screw; COTS; Slip ring; main_base; 3D Printed; slicon non_slip 10x2mm; MakerStorage LLC.

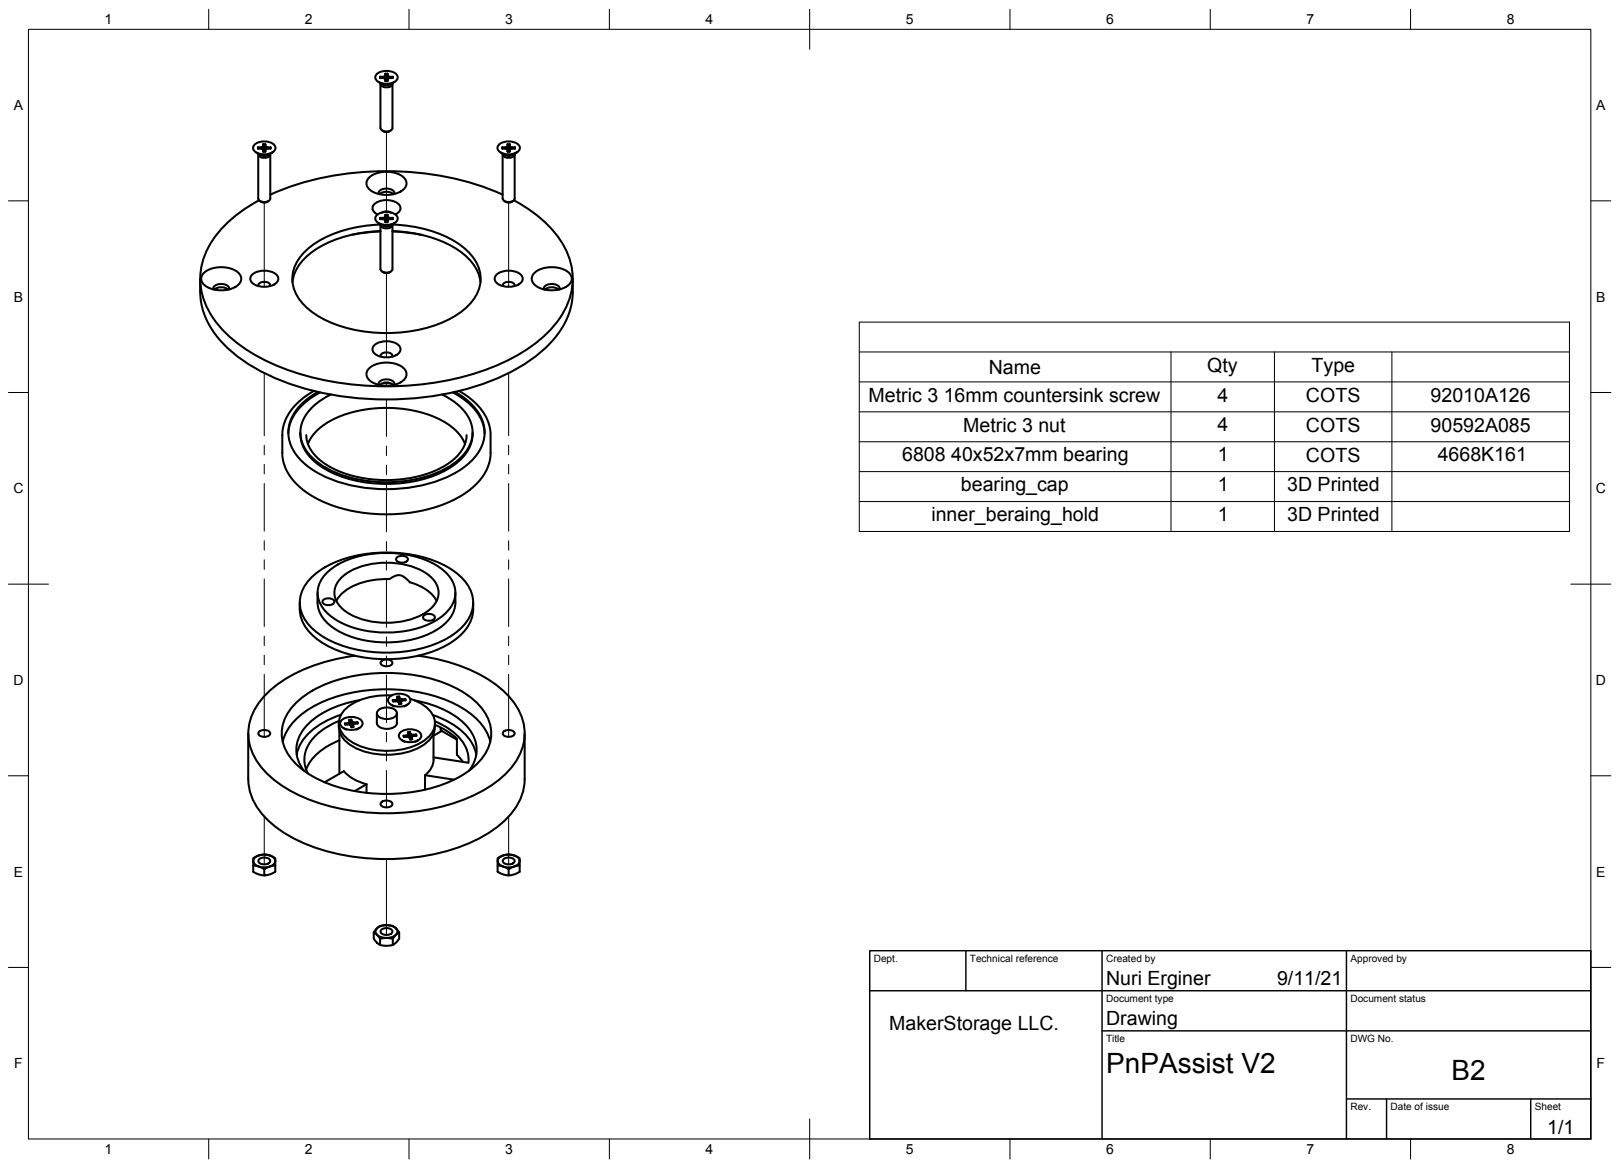
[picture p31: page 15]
Dept.; Technical reference; Created by; Approved by; Document type; Document status; Title; DWG No.; Drawing; PnPAssist V2; Nuri Erginer; Name; Qty; Type; Metric 3 16mm countersink screw; COTS; Metric 3 nut; 6808 40x52x7mm bearing; bearing_cap; 3D Printed; inner_beraing_hold; MakerStorage LLC.

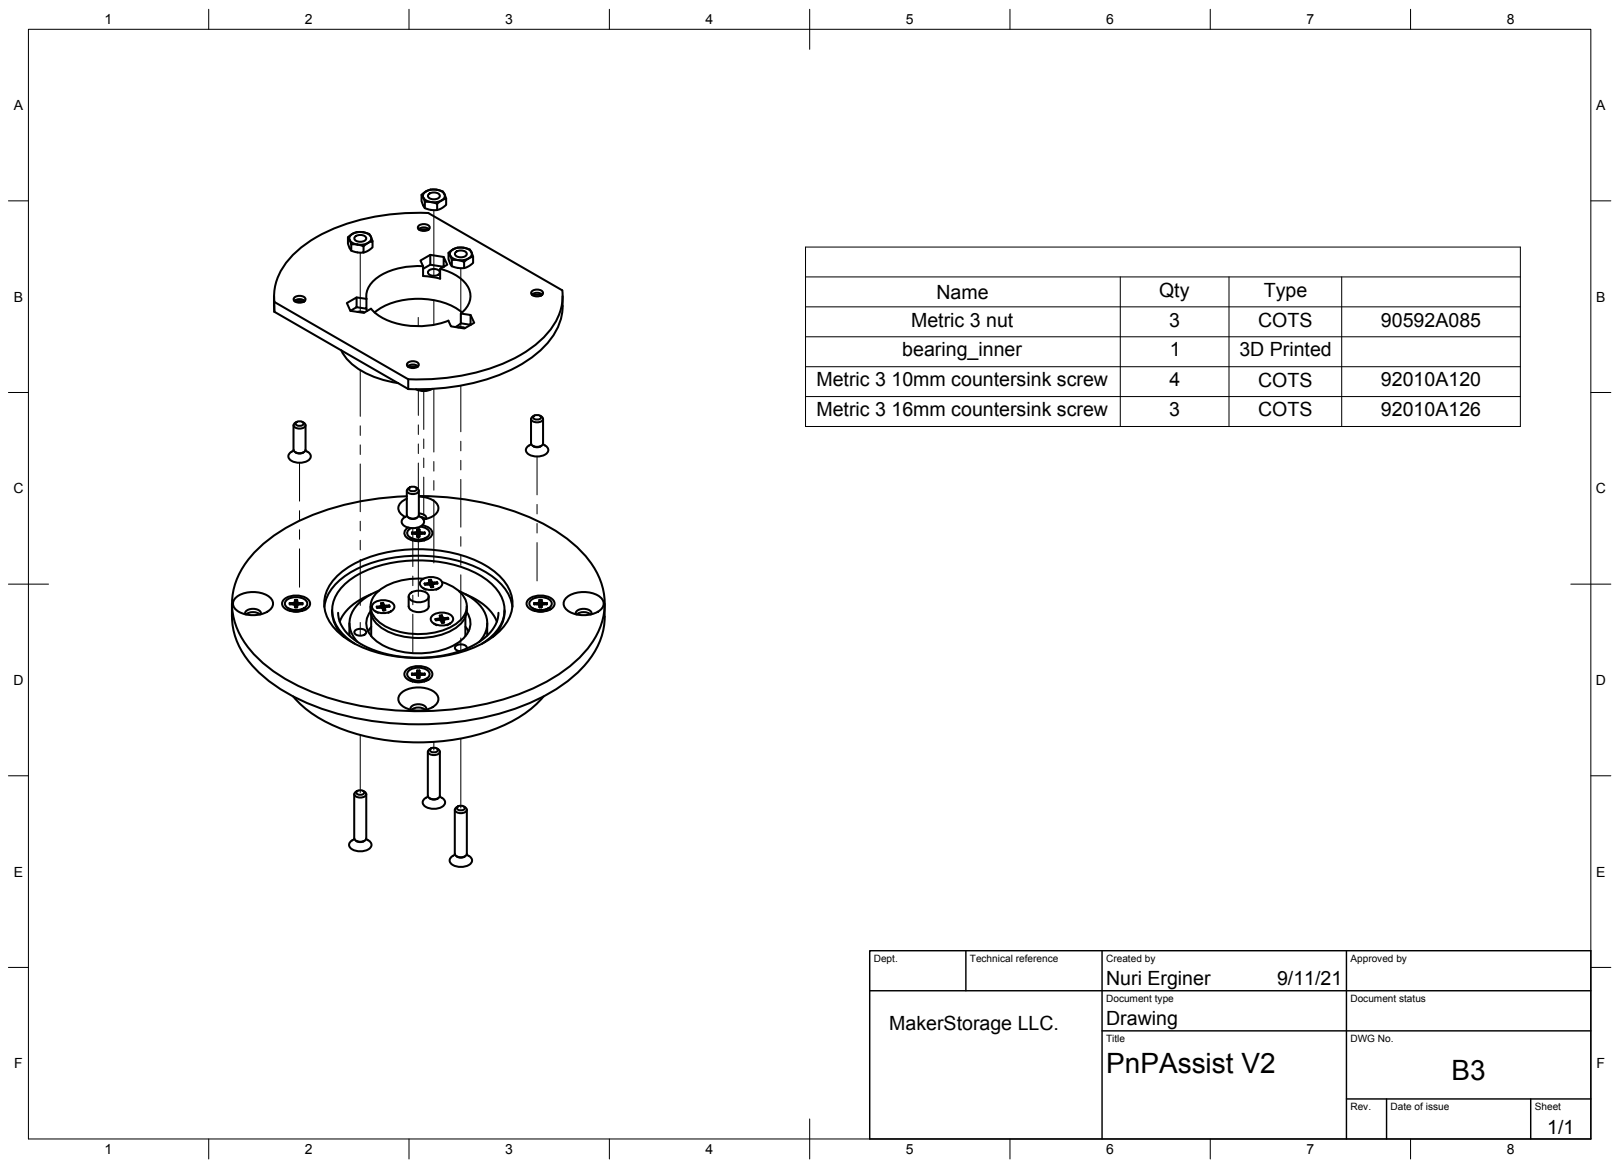
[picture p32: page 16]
Dept.; Technical reference; Created by; Approved by; Document type; Document status; Title; DWG No.; Drawing; PnPAssist V2; Nuri Erginer; Name; Qty; Type; Metric 3 nut; COTS; bearing_inner; 3D Printed; Metric 3 10mm countersink screw; Metric 3 16mm countersink screw; MakerStorage LLC.

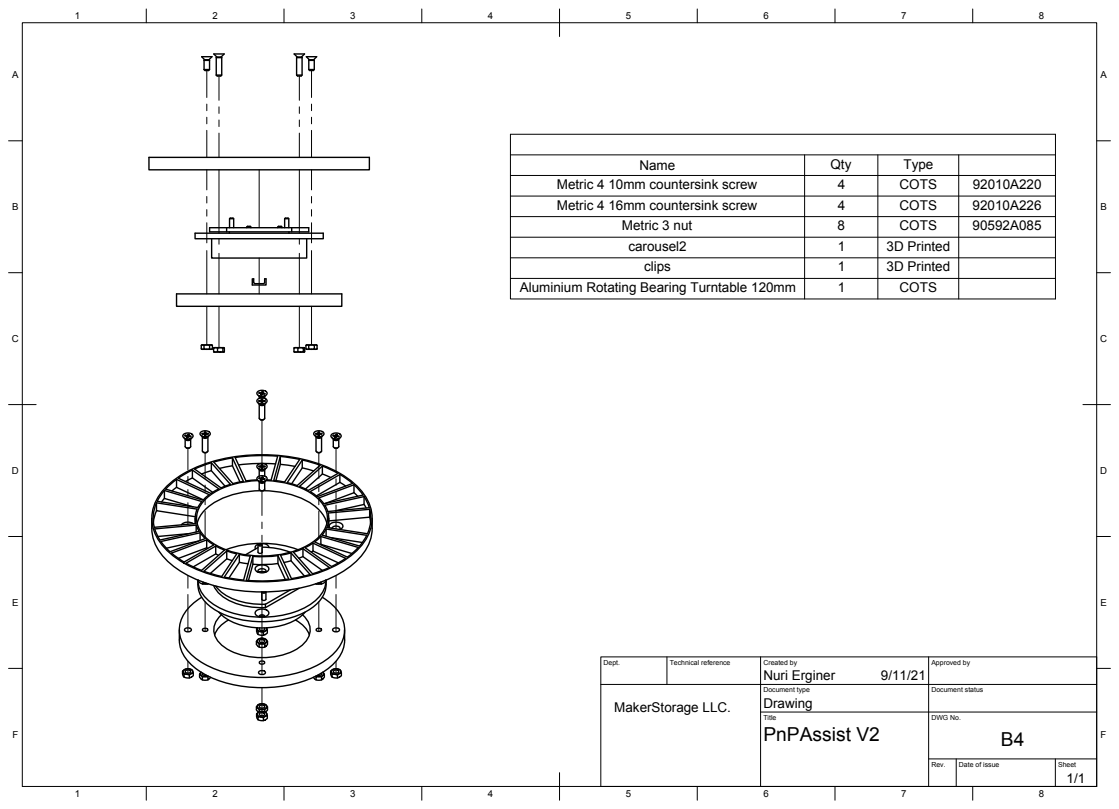
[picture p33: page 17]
Dept.; Technical reference; Created by; Approved by; Document type; Document status; Title; DWG No.; Drawing; PnPAssist V2; Nuri Erginer; Name; Qty; Type; Metric 4 10mm countersink screw; COTS; Metric 4 16mm countersink screw; Metric 3 nut; carousel2; 3D Printed; clips; Aluminium Rotating Bearing Turntable 120mm; MakerStorage LLC.

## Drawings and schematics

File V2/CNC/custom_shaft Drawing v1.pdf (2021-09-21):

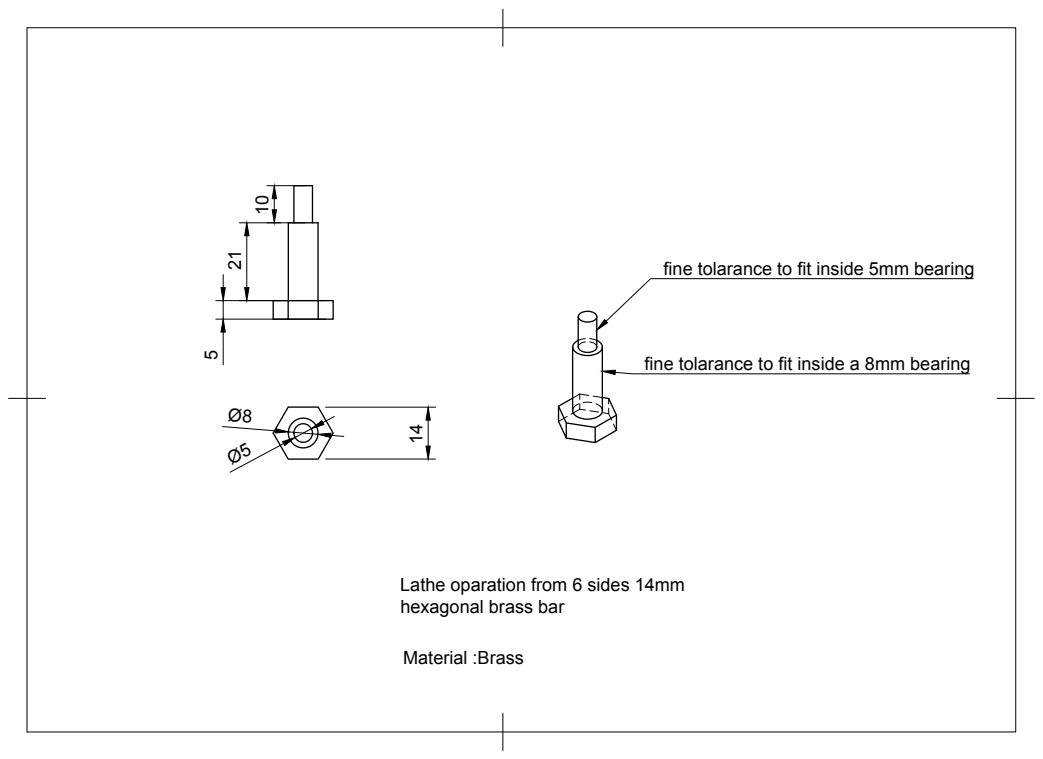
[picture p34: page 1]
Material :Brass

fine tolarance to fit inside 5mm bearing

fine tolarance to fit inside a 8mm bearing

Lathe oparation from 6 sides 14mm
hexagonal brass bar

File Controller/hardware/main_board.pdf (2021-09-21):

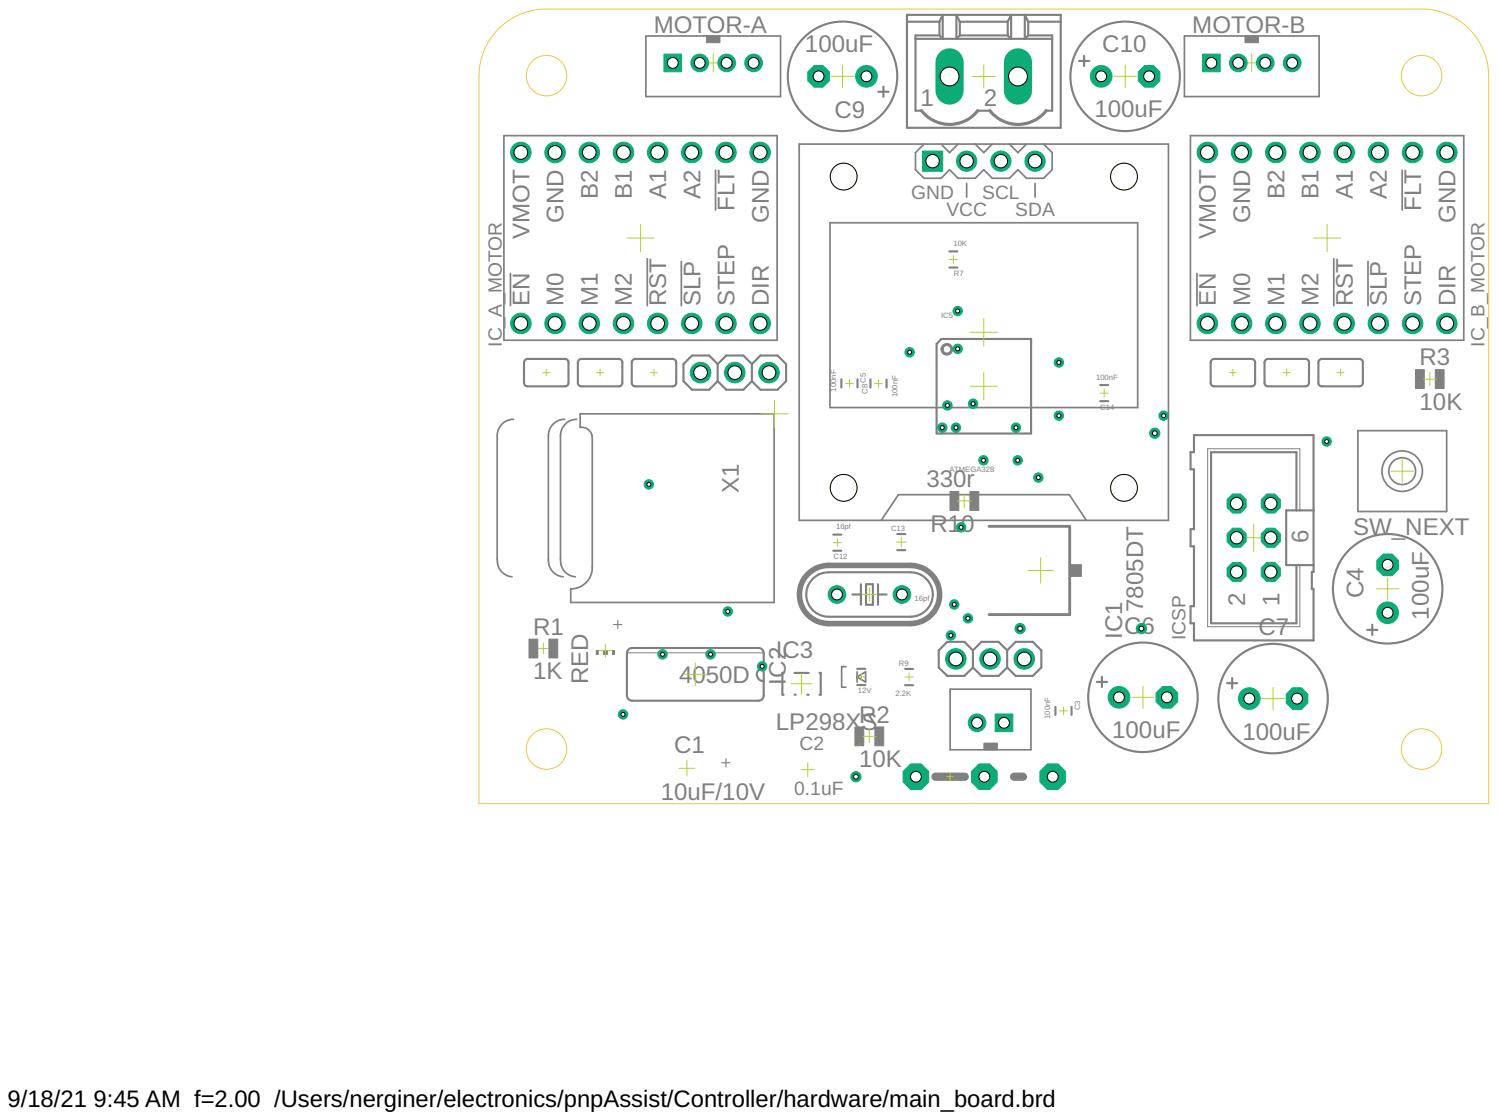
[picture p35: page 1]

9/18/21 9:45 AM f=2.00 /Users/nerginer/electronics/pnpAssist/Controller/hardware/main_board.brd

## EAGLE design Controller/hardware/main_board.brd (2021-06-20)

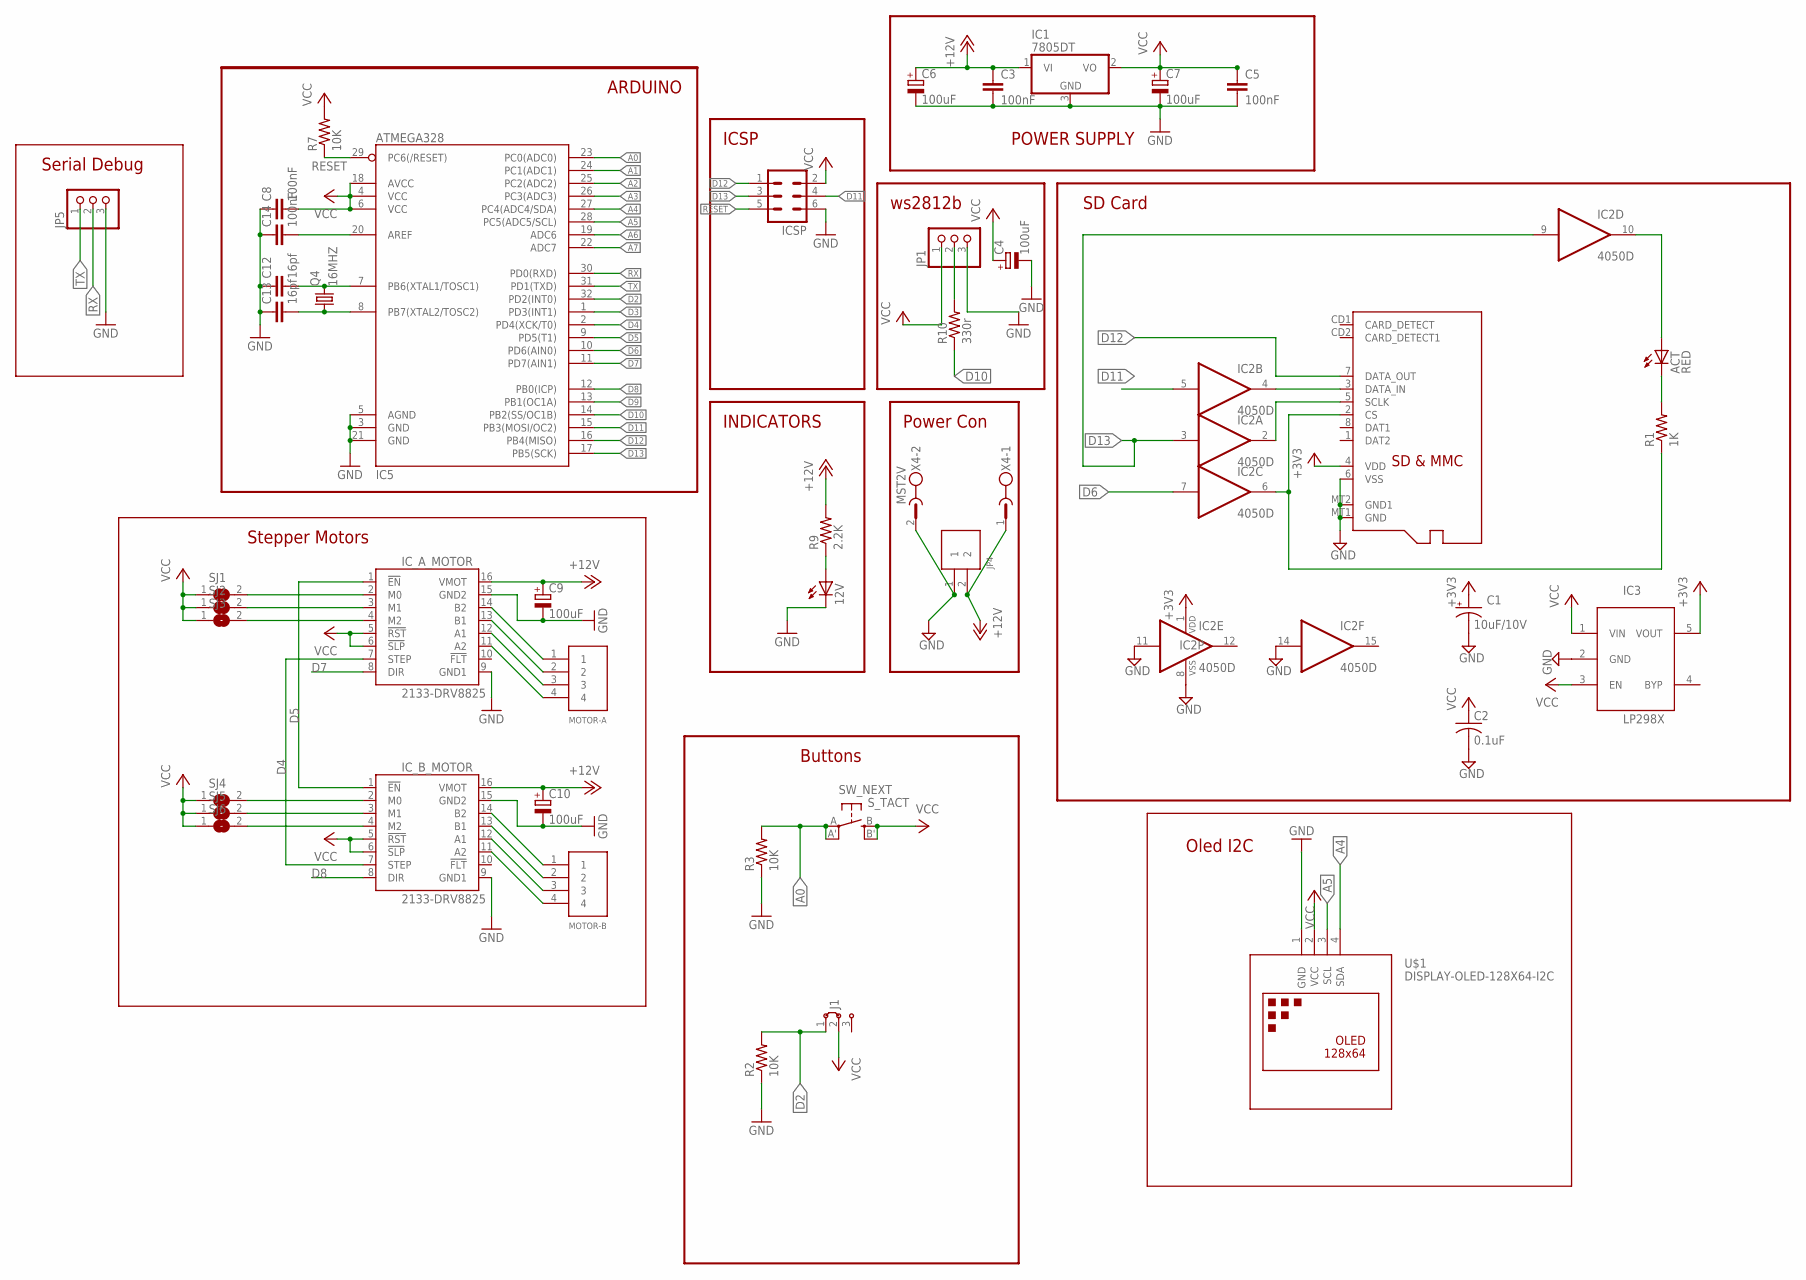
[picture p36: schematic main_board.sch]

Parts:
12V: LED0805; LED-0805
ACT: RED; CHIP-LED0805
C1: 10uF/10V; A/3216-18R
C2: 0.1uF; C0805K
C3, C5, C8, C14: 100nF; 0805
C4, C6, C7, C9, C10: 100uF; E3,5-8
C12, C13: 16pf; 0805
IC1: 7805DT; TO252
IC2: 4050D; SO16
IC3: LP298XS; SOT23-5L
IC5: ATMEGA328; TQFP32-08
ICSP: ML6
IC_A_MOTOR: 2133-DRV8825; DRV8825
IC_B_MOTOR: 2133-DRV8825; DRV8825
J1: J2X5MM; 05C
JP1, JP5: PINHD-1X3; 1X03
JP4: 2PIN; B2B-PH-K-S
MOTOR-A: 4PIN; B4B-PH-K-S
MOTOR-B: 4PIN; B4B-PH-K-S
Q4: 16MHZ; HC49/S
R1: 1K; R0805
R2, R3: 10K; R0805
R7: 10K; 0805
R9: 2.2K; 0805
R10: 330r; R0805
SJ1, SJ2, SJ3, SJ4, SJ5, SJ6: SJ
SW_NEXT: S_TACT; EVQ-Q2
U$1: DISPLAY-OLED-128X64-I2C
X1: MICROSD
X4: MST2V; MSTBV2

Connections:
+3V3: C1.+, IC2.1 (VDD), IC3.5 (VOUT), X1.4 (VDD)
+12V: C3.1, C6.+, C9.+, C10.+, IC1.1 (VI), IC_A_MOTOR.16 (VMOT), IC_B_MOTOR.16 (VMOT), JP4.2, R9.2, X4.1
A0: IC5.23 (PC0(ADC0)), R3.2, SW_NEXT.A, SW_NEXT.A' (P1)
A1: IC5.24 (PC1(ADC1))
A2: IC5.25 (PC2(ADC2))
A3: IC5.26 (PC3(ADC3))
A4: IC5.27 (PC4(ADC4/SDA)), U$1.4 (SDA)
A5: IC5.28 (PC5(ADC5/SCL)), U$1.3 (SCL)
A6: IC5.19 (ADC6)
A7: IC5.22 (ADC7)
D2: IC5.32 (PD2(INT0)), J1.1, R2.2
D3: IC5.1 (PD3(INT1))
D4: IC5.2 (PD4(XCK/T0)), IC_A_MOTOR.7 (STEP), IC_B_MOTOR.7 (STEP)
D5: IC5.9 (PD5(T1)), IC_A_MOTOR.1 (!EN), IC_B_MOTOR.1 (!EN)
D6: IC2.7 (I), IC5.10 (PD6(AIN0))
D7: IC5.11 (PD7(AIN1)), IC_A_MOTOR.8 (DIR)
D8: IC5.12 (PB0(ICP)), IC_B_MOTOR.8 (DIR)
D9: IC5.13 (PB1(OC1A))
D10: IC5.14 (PB2(SS/OC1B)), R10.1
D11: IC2.5 (I), IC5.15 (PB3(MOSI/OC2)), ICSP.4
D12: IC5.16 (PB4(MISO)), ICSP.1, X1.7 (DATA_OUT)
D13: IC2.3 (I), IC2.9 (I), IC5.17 (PB5(SCK)), ICSP.3
GND: 12V.C, C1.-, C2.2, C3.2, C4.-, C5.2, C6.-, C7.-, C8.1, C9.-, C10.-, C12.1, C13.1, C14.1, IC1.3 (GND), IC2.8 (VSS), IC2.11 (I), IC2.14 (I), IC3.2 (GND), IC5.3 (GND), IC5.5 (AGND), IC5.21 (GND), ICSP.6, IC_A_MOTOR.9 (GND1), IC_A_MOTOR.15 (GND2), IC_B_MOTOR.9 (GND1), IC_B_MOTOR.15 (GND2), JP1.3, JP4.1, JP5.3, R2.1, R3.1, U$1.1 (GND), X1.6 (VSS), X1.MT1 (GND), X1.MT2 (GND1), X4.2
unnamed: ACT.A, IC2.10 (O)
unnamed: IC2.2 (O), X1.5 (SCLK)
unnamed: IC2.6 (O), R1.1, X1.2 (CS)
unnamed: ACT.C, R1.2
unnamed: IC2.4 (O), X1.3 (DATA_IN)
unnamed: JP1.2, R10.2
unnamed: IC_A_MOTOR.2 (M0), SJ1.2
unnamed: IC_A_MOTOR.3 (M1), SJ2.2
unnamed: IC_A_MOTOR.4 (M2), SJ3.2
unnamed: IC_B_MOTOR.2 (M0), SJ4.2
unnamed: IC_B_MOTOR.3 (M1), SJ5.2
unnamed: IC_B_MOTOR.4 (M2), SJ6.2
unnamed: IC_A_MOTOR.14 (B2), MOTOR-A.1
unnamed: IC_A_MOTOR.13 (B1), MOTOR-A.2
unnamed: IC_A_MOTOR.12 (A1), MOTOR-A.3
unnamed: IC_A_MOTOR.11 (A2), MOTOR-A.4
unnamed: IC_B_MOTOR.14 (B2), MOTOR-B.1
unnamed: IC_B_MOTOR.13 (B1), MOTOR-B.2
unnamed: IC_B_MOTOR.12 (A1), MOTOR-B.3
unnamed: C14.2, IC5.20 (AREF)
unnamed: IC_B_MOTOR.11 (A2), MOTOR-B.4
unnamed: 12V.A, R9.1
unnamed: C12.2, IC5.7 (PB6(XTAL1/TOSC1)), Q4.2
unnamed: C13.2, IC5.8 (PB7(XTAL2/TOSC2)), Q4.1
RESET: IC5.29 (PC6(/RESET)), ICSP.5, R7.1
RX: IC5.30 (PD0(RXD)), JP5.2
TX: IC5.31 (PD1(TXD)), JP5.1
VCC: C2.1, C4.+, C5.1, C7.+, C8.2, IC1.2 (VO), IC3.1 (VIN), IC3.3 (EN), IC5.4 (VCC), IC5.6 (VCC), IC5.18 (AVCC), ICSP.2, IC_A_MOTOR.5 (!RST), IC_A_MOTOR.6 (!SLP), IC_B_MOTOR.5 (!RST), IC_B_MOTOR.6 (!SLP), J1.2, JP1.1, R7.2, SJ1.1, SJ2.1, SJ3.1, SJ4.1, SJ5.1, SJ6.1, SW_NEXT.B (S), SW_NEXT.B' (S1), U$1.2 (VCC)

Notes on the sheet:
ICSP
ARDUINO
INDICATORS
POWER SUPPLY
Power Con
SD Card
Buttons
ws2812b
Oled I2C
Stepper Motors
Serial Debug

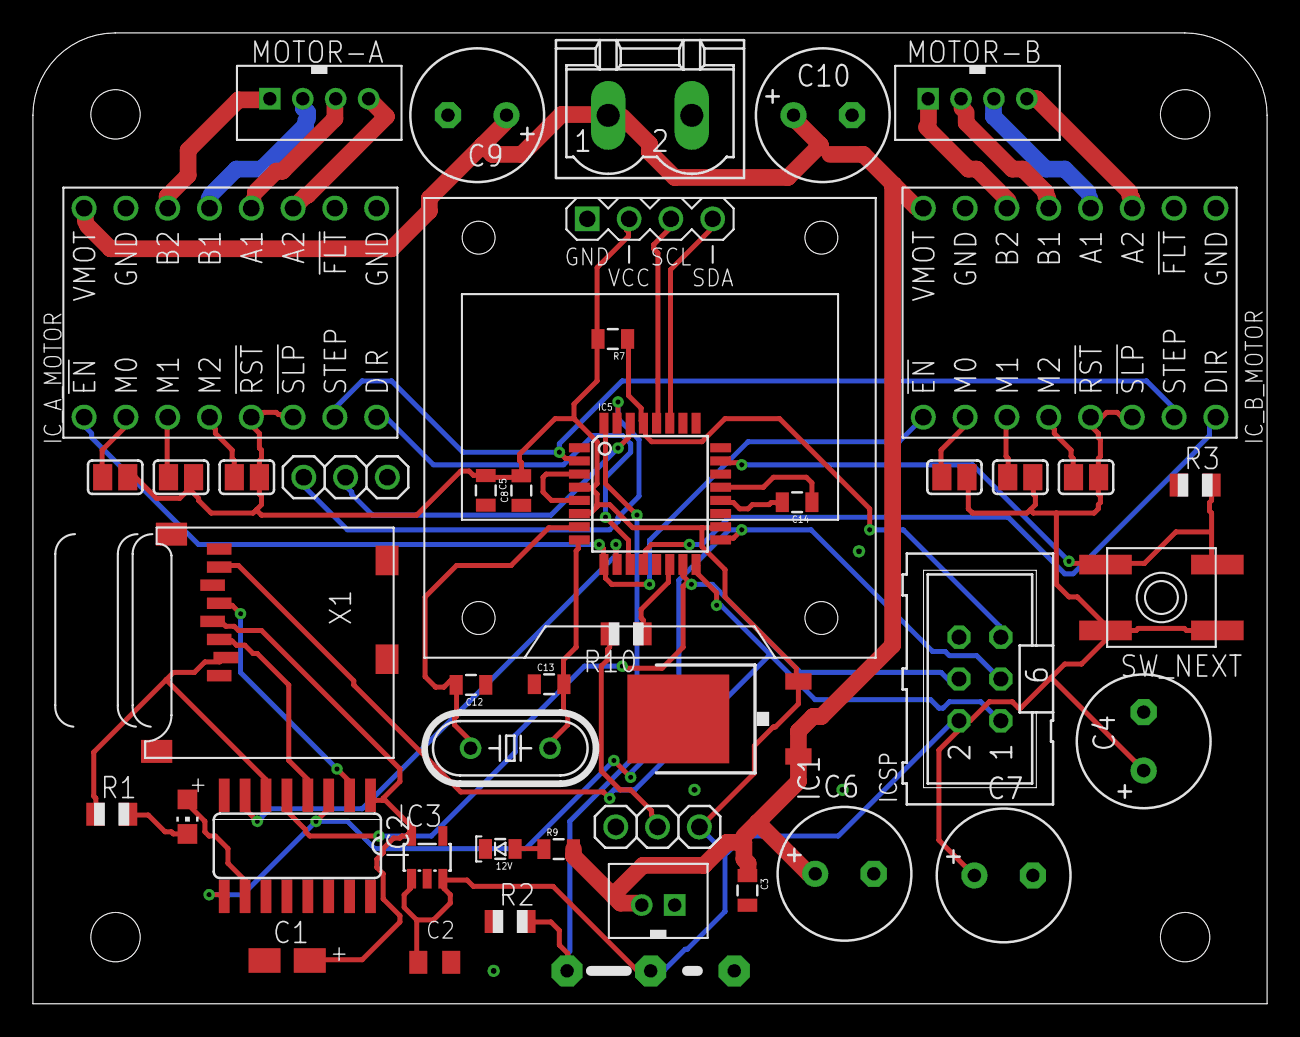
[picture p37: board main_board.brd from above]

Board: 2 copper layers, 75.0 x 59.0 mm, 45 parts (0 on the bottom side), 44 nets.

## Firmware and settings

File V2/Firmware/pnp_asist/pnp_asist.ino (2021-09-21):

//    PNP Asist Firmware ver0.9
//    Designed for use on the Arduino UNO
//    Copyright 2021 2022 MakerStorage LLC.
//   
//    LICENSE INFORMATION
//
//    This work is licensed under the:
//    "Creative Commons Attribution-NonCommercial-ShareAlike 3.0 Unported License"
//
//    To view a copy of this license, visit:
//      http://creativecommons.org/licenses/by-nc-sa/3.0/deed.en_US
//
//    For updates and to download the lastest version, visit:
//      http://github.com/MakerStorage or
//      http://pnpassist.com
//
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

#include <math.h>
#include <TimerOne.h>
#include "U8glib.h"
#include <SD.h>
#include <SPI.h>


#define DEBUG

// input pnp File
File pnpFile;

// we read the line from file to this var
String fileLine;
boolean SDfound;


// parsing vars
char fullMsg[ 120 ];
const uint8_t MAX_FIELD_COUNT = 6;
char *field[ MAX_FIELD_COUNT ];
uint8_t fieldCount;

// field[0] name of the component C1
// field[1] X coordinate
// field[2] Y coordinate
// field[3] Angle
// field[4] component value
// field[5] component package

//oled
U8GLIB_SSD1306_128X64 u8g(U8G_I2C_OPT_NONE | U8G_I2C_OPT_DEV_0);


// display buffer
char bufferX [20];
char bufferY [20];
char bufferZ [20];


//#define SPEED 2000
#define StepPerMM 160 


//Result  Resolution  Teeth Step angle  Stepping  Belt
//160.00  6.25micron  20    1.8°        1/32th    2mm


// Stepper Motors Outputs
#define ENABLE 5 // same out for 2 motors
#define STEP   4 // same out for 2 motors
#define A_DIR    8
#define B_DIR    7

// Movement states
#define MOVING    0
#define ARRIVED   1


//length of y axis
//#define MAX_Y_LENGTH 250

#define CENTER_Y_OFFSET 5020


#define AXIS_OFFSET 30 // where your 0,0 away from both axis v2

#define SEARCH_HOME_SWITCH_SPEED 1500
#define SLOW_HOMING_SPEED 200

// homing trigered flag
volatile bool FindZero = false;

//SD CSPIN
#define CSPIN 6

//button 
#define NEXT_BUTTON_PIN A0

//button y home switch
const byte yHomePin = 2;



// Stepper speeds in RPM
int iDriveSpeed = 400;


volatile long CurPos         = 0;
volatile long TargetPos      = 0;

// Motion state variables
volatile int Status     = ARRIVED;

volatile int lastStepPulse   = LOW;


float mAngle = 0; //in degrees
float mRadius = 0; 
float eskiAngle = 90; // starting angle is 90
float eskiRadius = 0; // offsets are 22   so sqr(22*22+22*22) = 31.113;

void waitForButton(){ 
 // int val = digitalRead(NEXT_BUTTON_PIN);
  
  //Wait for the button
  
  while(!digitalRead(NEXT_BUTTON_PIN)) {
   // val = digitalRead(NEXT_BUTTON_PIN);
   delay(10); 
  }
  
  delay(10);  
}


void CalcAngleRadius(float x, float y){
  mAngle = atan2(y, x) * 180/PI; // use atan2 to get the quadrant
  Serial.print("CalcAngleRadius mAngle: ");
  Serial.println(mAngle);
  mRadius = sqrt((x * x) + (y * y));
  Serial.print("mRadius: ");
  Serial.println(mRadius);
  
}

void don(float angle){
  float polarXMove = round(angle * 0.11111111111111111 * StepPerMM);//20T with 2mm belt pitch it is 40mm per rotation (360 deg)
  // so 40/360 = 0.111111 rounding 
  G1X(polarXMove);
  
  //String l="G1X"+String(polarXMove)+"F"+String(SPEED);
  //Serial.println(l);
}

void git(float y){

  float distance = round(y * StepPerMM);
  G1Y(distance);
 
  //String l="G1Y"+String(y)+"F"+String(SPEED);
  //Serial.println(l);
}

void gonder(){
      
      CalcAngleRadius((atof(field[1])-AXIS_OFFSET),(atof(field[2])-AXIS_OFFSET)); //x,y
      float mydon = eskiAngle - mAngle;
      don(mydon);
      float mygit = mRadius - eskiRadius;
      git(mygit);
      eskiAngle = mAngle;
      eskiRadius = mRadius;
}


void setup() {

  Timer1.initialize(150000/iDriveSpeed);
  // attach the motor intrupt service routine here
  Timer1.attachInterrupt( updateMotors ); 
  setMotorSpeed(iDriveSpeed);
  StepRelease();
 
  Serial.begin(115200);

  //next button as input
  pinMode(NEXT_BUTTON_PIN, INPUT);

  pinMode(yHomePin, INPUT);
  attachInterrupt(digitalPinToInterrupt(yHomePin), HomeSwitchReached, RISING);



              // homing
              sprintf(bufferX, "MakerStorage");
              sprintf(bufferY, "Homing......");
              sprintf(bufferZ, "PnPAssist");
              
              HomeY(-3000, SEARCH_HOME_SWITCH_SPEED);
              delay(100);

              // move back alittle
              git (10);
              delay(100);

              // seach home slowly
              HomeY(-110, SLOW_HOMING_SPEED);
              delay(100);

              
              // move back alittle for the rotary notch
              git (2);
              delay(100);
              
              // homing Rotary Axis 
              HomePolar(-365, SEARCH_HOME_SWITCH_SPEED*0.50); // negative because it indicate the direction where to rotate
              delay(100);

              // turn back alittle
              don (20);
              delay(100);

              // seach home slowly
              HomePolar(-100, SLOW_HOMING_SPEED*0.50);
              delay(100);

            
              // Goto Center
              setMotorSpeed(iDriveSpeed);
              G1Y(CENTER_Y_OFFSET); // goto center

              // Set Angle to 0 bumper conpansation
              don (-3);
       
              // we are all at home :)
              // init to 0

     //        mAngle = 0; //in degrees
     //        mRadius = 0; 
    //         eskiAngle = 0; // starting angle is 45
    //         eskiRadius = 0; // offsets are 22 for both x and y  so sqr(22*22+22*22) = 31.113;


          
 
  sprintf(bufferX, "MakerStorage");
  sprintf(bufferY, "----------");
  sprintf(bufferZ, "PnPAssist");

  //logo display delay
  oledPrint();
  delay(1000);

  //Sd init
  if (SDfound == 0) {
    if (!SD.begin(CSPIN)) {
      Serial.print("The SD card cannot be found");
      while(1);
    }
  }
  SDfound = 1;
  pnpFile = SD.open("pnp.txt",FILE_READ);

  if (!pnpFile) {
    Serial.print("The text file cannot be opened");
    while(1);
  }

  sprintf(bufferX, "MakerStorage");
  sprintf(bufferY, "Ready!");
  sprintf(bufferZ, "PnPAssist");

  oledPrint();


}//setup

void HomeY(float distance, float Speed){
  FindZero = true;
  setMotorSpeed(Speed);
  git(distance);  
}

void HomePolar(float angle, float Speed){
  FindZero = true;
  setMotorSpeed(Speed);
  don(angle);  
}


void HomeSwitchReached(){ //Interrupt function
  if(FindZero) {
    FindZero = false;
    Status = ARRIVED;
    CurPos = 0;
    TargetPos = 0;
  }
}

void loop() {
  while (!pnpFile.available()) { // nothing to read
     pnpFile.close();
     sprintf(bufferZ, "FINISHED!!!"); // FINISHED 
     oledPrint();
     digitalWrite(ENABLE, HIGH);
     while(true){}//Program Ended!
  }
  
  waitForButton();
    
  fileLine = pnpFile.readStringUntil('\n');
  parseCommand(fileLine+" ");

  #ifdef DEBUG
    Serial.println ("f0: " + String(field[0]));
    Serial.println ("f1: " + String(field[1]));
    Serial.println ("f2: " + String(field[2]));
    Serial.println ("f3: " + String(field[3]));
    Serial.println ("f4: " + String(field[4]));
    Serial.println ("f5: " + String(field[5]));
  #endif
  
  // display line contents
  sprintf(bufferX, field[0]); // component name ,
  sprintf(bufferY, "%s/%s",field[4],field[5]); // component value,package
  sprintf(bufferZ, "MOVING..."); // moving
  oledPrint();
  
  gonder(); // move the motors

  sprintf(bufferZ, "ARRIVED"); // ARRIVED
 
  oledPrint();

}//loop

void G1X(long pulseCount){
  //X rotation axis and must turn oposite directions
  if (pulseCount > 0) { //direction
    digitalWrite(A_DIR, HIGH);
    digitalWrite(B_DIR, HIGH);
  }else {
    digitalWrite(A_DIR, LOW);
    digitalWrite(B_DIR, LOW);   
  }

  TargetPos = abs(pulseCount); 
  Status = MOVING;

  while(Status == MOVING){
    sprintf(bufferZ, "MOVING..."); // ARRIVED
    oledPrint();
  }; // wait for move complate
  

  
  CurPos = 0;
  TargetPos = 0;
  
}

void G1Y(long pulseCount){
  //Y linear axis and must turn same directions
  if (pulseCount < 0) { //direction
    digitalWrite(A_DIR, HIGH);
    digitalWrite(B_DIR, LOW);
  }else {
    digitalWrite(A_DIR, LOW);
    digitalWrite(B_DIR, HIGH);   
  }

  TargetPos = abs(pulseCount); 
  Status = MOVING;

  while(Status == MOVING){
    sprintf(bufferZ, "MOVING..."); // ARRIVED
    oledPrint();
  }; // wait for move complate
  

  CurPos = 0;
  TargetPos = 0;
  
}




// Called 800 times per second when y speed is 120 rpm
// Called 66.7 times per second when y speed is 10 rpm
// Called 933.3 times per second when y speed is 140 rpm

void updateMotors()
{
  // For both motors
  if (TargetPos > CurPos) { // We need to move 
    Step();
  }
  
  if ((CurPos == TargetPos)&&(Status==MOVING))
  {
    // we are reached the destination
    StepRelease();
    Status = ARRIVED;
  }
  
}

///////////////////////////////////////////////////////

///////////////////////////////////////////////////////
//
// Step once, update position
//
void Step(){
  if(lastStepPulse == LOW){
    digitalWrite(ENABLE, LOW);
    digitalWrite(STEP, HIGH);
    lastStepPulse = HIGH;
  }
  else {
    digitalWrite(ENABLE, LOW);
    digitalWrite(STEP, LOW);
    lastStepPulse = LOW;
    CurPos++;
  }
}

///////////////////////////////////////////////////////

///////////////////////////////////////////////////////
//
// Release the Stepper Motors
//
void StepRelease(){
 // digitalWrite(ENABLE, HIGH);
  digitalWrite(A_DIR, LOW);
  digitalWrite(B_DIR, LOW);
  digitalWrite(STEP, LOW);
  lastStepPulse = LOW;
}

///////////////////////////////////////////////////////

// Reset the timer for stepper motor updates to
// control rpm
void setMotorSpeed(int iRPM){
  Timer1.setPeriod(150000/iRPM);
}

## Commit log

2021-06-14 homing min
2021-07-15 Next Button Code Changed
2021-07-15 two axis homing
2021-07-18 machine y offset set after new bearing
2021-07-22 3D Files
    [ayak_ust_base.stl, ayak_ust_base_B.stl, bilezik.stl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]
2021-07-24 main gear design v2
    [lead t8 2mm pitch-duz_hex v1.stl, main_board.dxf, son_disli_kavisli v2.stl]
2021-07-26 2d files added
    [bottom_sheet_metal.dxf, top_sheet_metal.dxf]
2021-07-26 Dxf version update
    [bottom_sheet_metal.dxf, top_sheet_metal.dxf]
2021-07-29 knobs added to 3d files
    [pnp_assist_tutac v1.stl]
2021-07-29 step files added to 3d files
    [ayak_ust_base.stl, ayak_ust_base.stp, ayak_ust_base_B.stl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]
2021-08-30 rulman_tut_orta file updated
    [rulman_tut_orta.stl]
2021-09-05 delay added to button wait code
2021-09-21 v2 stl files, assembly_manual_2d files_custom_shaft added
    [alt_rulmanlik v13.stl, arabalik v16.stl, bearing_cap v2.stl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]
2021-09-22 step files added
    [alt_rulmanlik v13.step, alt_rulmanlik v13.stl, arabalik v16.step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]
2022-01-03 rotator updated
    [rotator4 v9.stl, rotator5.step, rotator5.stl]
2022-01-05 kicad plugin added

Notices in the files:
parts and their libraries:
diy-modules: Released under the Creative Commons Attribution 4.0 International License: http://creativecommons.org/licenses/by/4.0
